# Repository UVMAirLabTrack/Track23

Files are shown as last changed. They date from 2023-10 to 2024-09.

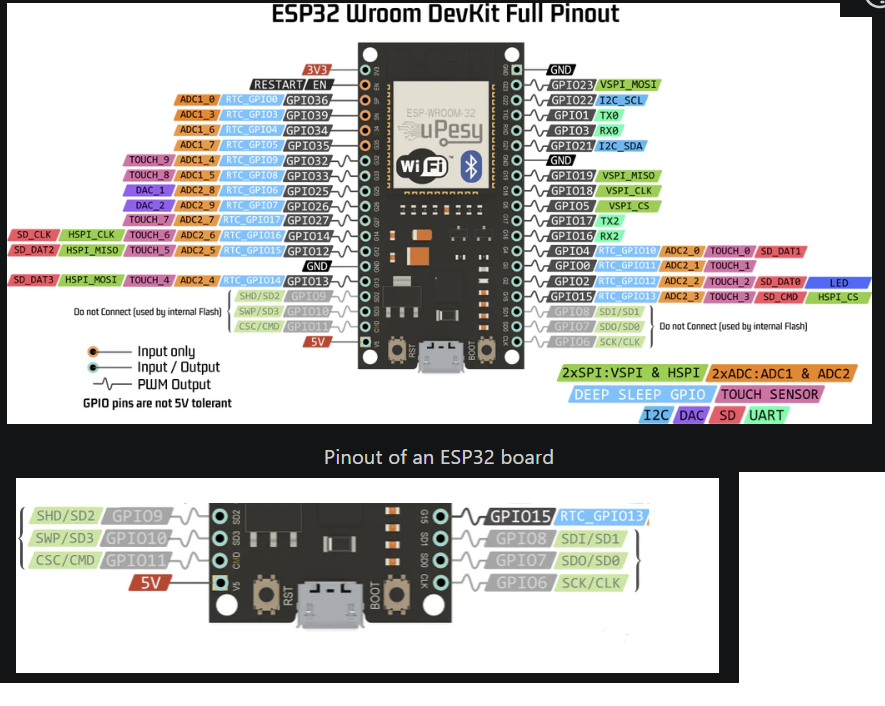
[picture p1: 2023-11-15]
InteractiveElements/Board Design and IO/ESP32GPIO.png

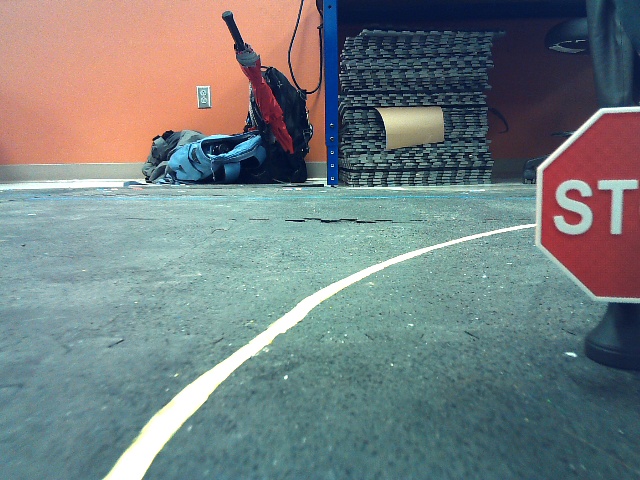
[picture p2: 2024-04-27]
Mid Process Stuff/Training Images/cut/stop (29).jpg

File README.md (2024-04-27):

# UVM SEED 2023 Track
 
## Repository for code and setup files associated with the 2023 UVM SEED Project for an urban track for autonomous cars

## File Structure

### A. Documentation
Look in here to find the detailed instructions on how to build and run the track system. As well as more in depth information as to the system's function

- 
- 
- 
- 

### 3D modelling

Under this folder are organized locations for all the .stl files used to create the various printed elements. 

### Interactive Elements

Here you will find the Arduino IDE code files used for the ESP32 interactive element network.
Additionally Kicad format PCB's and schematics are located here.
The receiver for each interactive element utilizes the same PCB, with 4 RJ45 connectors and a single ESP32 Dev Module with 38 pins (WROOM- D or E)
The only change is which code file is flashed. 

Some previous versions utilizing pure serial connections have been left for adapability. The latest track build utilizes:

1. Stoplight
    - ESPnow_4way_4int.ino  
    - ESP_now_3Way.ino
2. Train Crossing
    - ESPNowTrain_Complete.ino
3. Sender
    - ESPnowSender.ino

With the sender node being connected via serial to the computer controlling the track, In this case a Raspberry Pi 4B 8GB model.

### CoreRaspbery 
is the ROS2 Workspace,

at present the code is designed to build into a Humble distro, however in testing the code can also be built for a Foxy distro.

### Setup Files 
contains some basic files to aid in deploying the Raspberry Pi track computer

### Car commands 
is a curated list of the terminal commands needed to operate specific functions of the Yahboom R2 car
Also contained within are some quality of life improvements to the deployment of the docker environment on the car, just some simple .sh files.

### Other Code

A series of files not directly part of the track functionality. Mostly a series of HSV decoders and Webcam Capture files 

### files not in a folder

the Dockerfiles in the main directory are intended to build a docker container to run all the ROS code, this is not intended for deployment on the PI as of this moment, instead it is intended as a complete package for the vizualizer node(s). At present, windows communication via WiFi is not functional due to additional networking constraints.

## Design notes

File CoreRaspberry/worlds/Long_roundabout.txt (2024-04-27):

Change_Color False
X_position 0.0
Y_position 0.0
Z_position 0.0
Quaternion_x 0.0
Quaternion_y 0.0
Quaternion_z 0.0
Quaternion_w 1.0
Scale_x 1.0
Scale_y 1.0
Scale_z 1.0
Color_r 1.0
Color_g 1.0
Color_b 1.0
Color_a 1.0
Lifetime_sec 0
Frame_locked False
Mesh_use_embedded_materials True
Frame_id map

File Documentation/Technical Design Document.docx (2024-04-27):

Technical Design Document

_____________________________________________________________________________________

Date | Revision | Release Notes
4/26/24 | 01 | Initial Release

# 1 Mechanical Documentation

## 1.1 System Level Assembly Drawing 1: Interactive Urban Track

The System Level Assembly drawing of the project is shown in Figure 1 from the “System Level Diagram v1.dwg”.

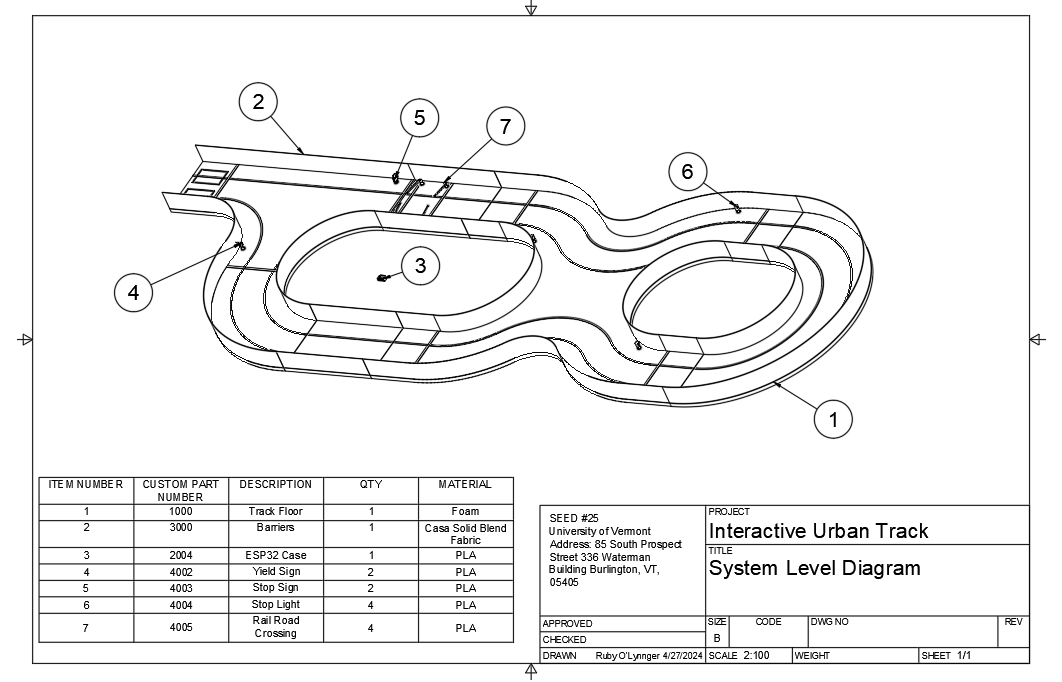
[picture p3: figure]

Figure 1 - System Level Assembly Drawing

## 1.2 System Level Bill of Materials

The System Level Bill of Materials is in Table 1, and also in the file “BOM.xlsx”.

Table 1 - Bill of Materials for Interactive Urban Track

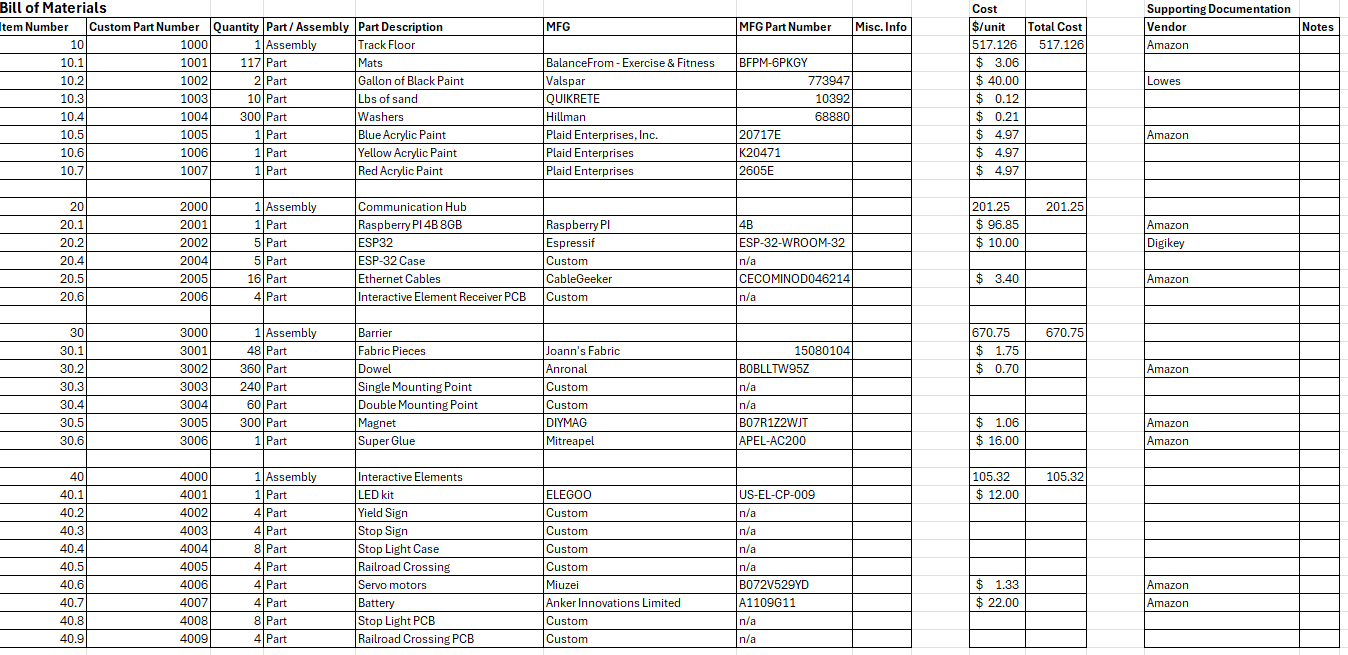
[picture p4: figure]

## 1.3 Part Drawings

### 1.3.1 Part 2004: ESP-32 Case

Part 2004: ESP-32 case is shown in Figure 2 from the file “ESP Controller Box Drawing.dwg”.

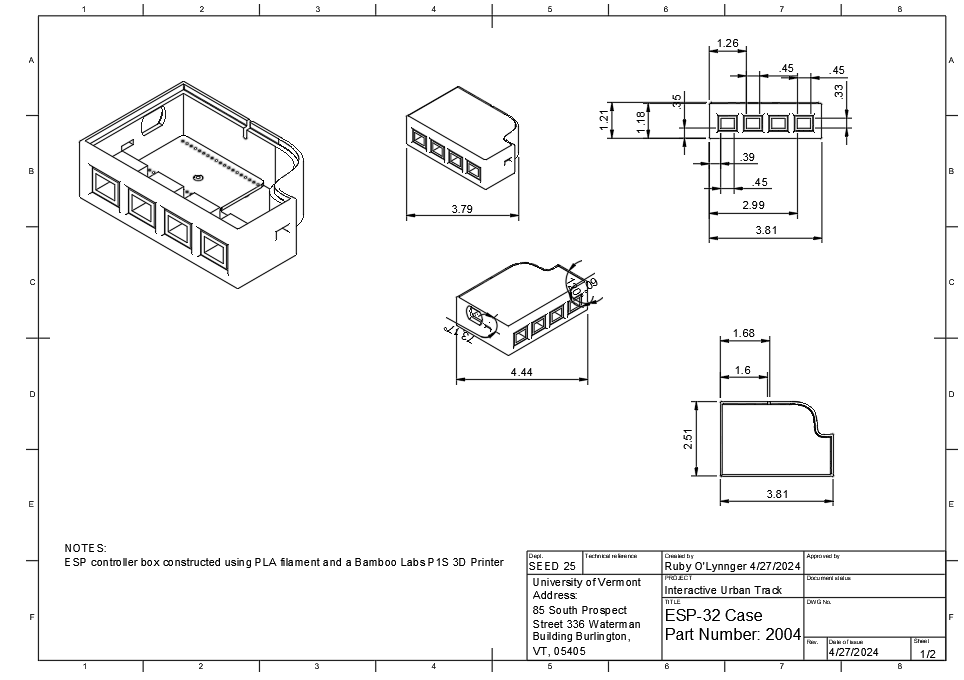
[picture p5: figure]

Figure 2 - ESP-32 Case Drawing

### 1.3.2 Part 3003: Single Mounting Point

Part 3003: Single Mounting Point is shown in Figure 3 from the file “Single Mounting Point Drawing v2.dwg”.

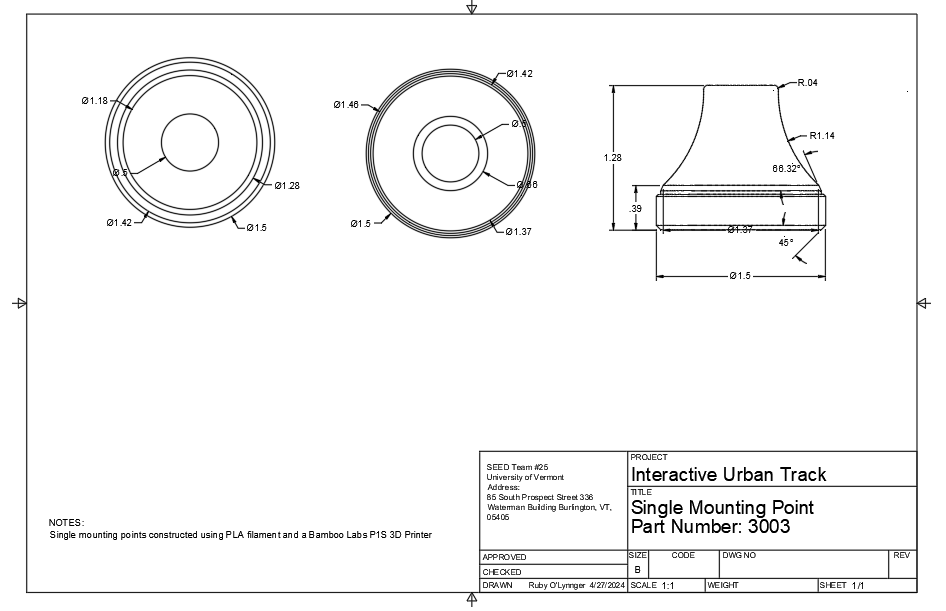
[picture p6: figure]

Figure 3 - Single Mounting Point Drawing

### 1.3.3 Part 3004: Double Mounting Point

Part 3004: Double Mounting Point is shown in Figure 4 from the file “Double Mounting Point Drawing v4.dwg”.

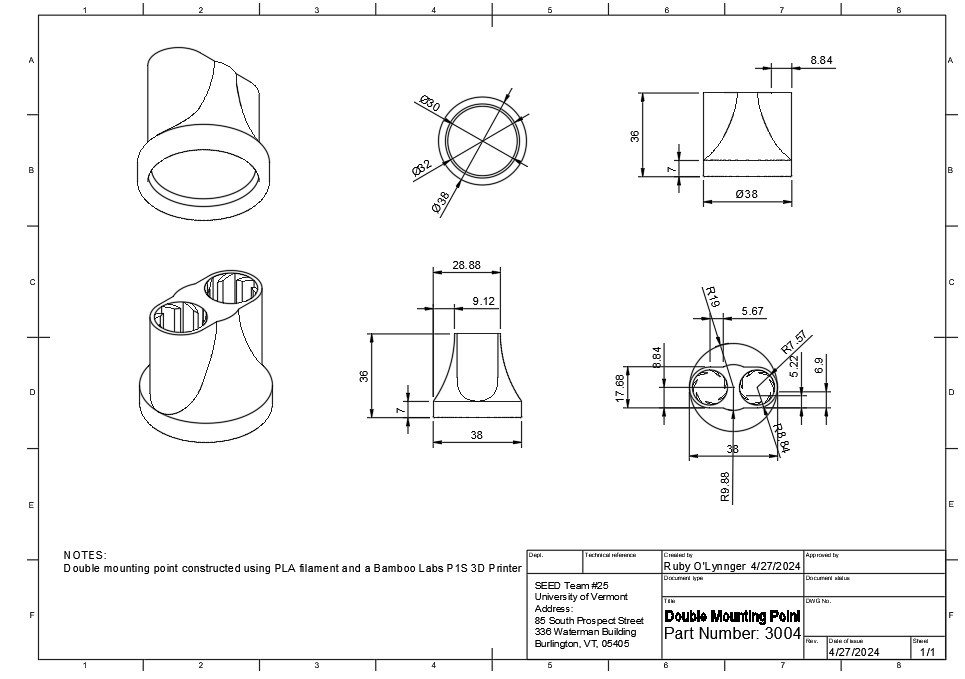
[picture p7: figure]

Figure 4 - Double Mounting Point Drawing

### 1.3.4 Part 4002: Yield Sign

Part 4002: Yield Sign is shown in Figure 5 from the file “Yield Sign Drawing.dwg”.

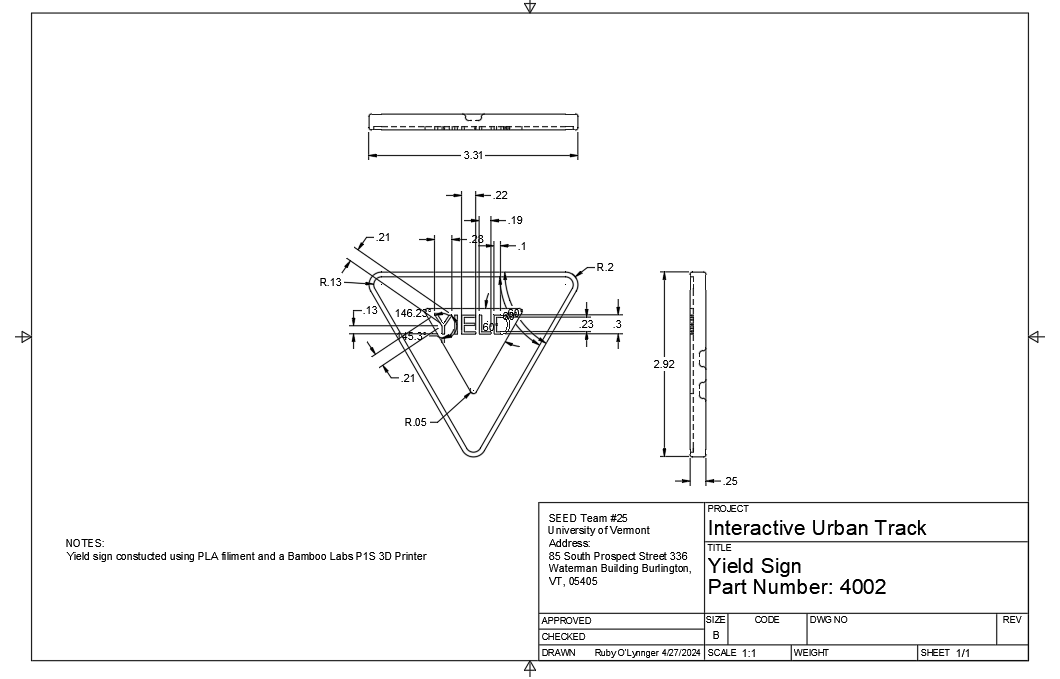
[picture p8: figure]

Figure 5 - Yield Sign Drawing

### 1.3.5 Part 4003: Stop Sign

Part 4003: Stop Sign is shown in Figure 6 from the file “Stop Sign Drawing.dwg”.

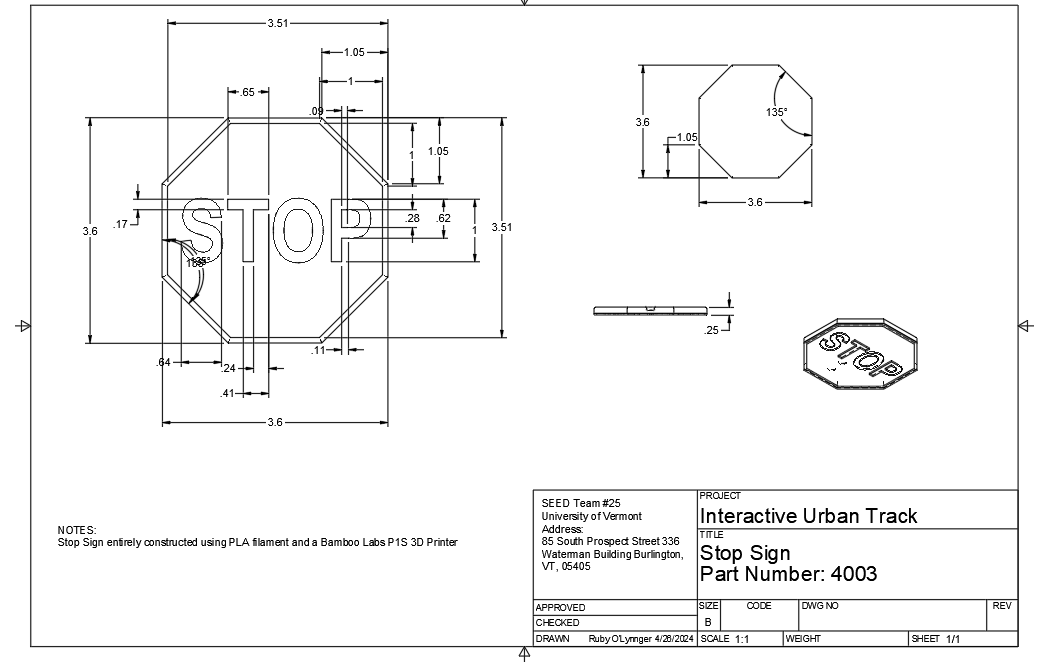
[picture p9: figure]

Figure 6 - Stop Sign Drawing

### 1.3.6 Part 4004: Stop Light

Part 4004: Stop Light is shown in Figure 7 from the file “Assembled Light Drawing v3.dwg”.

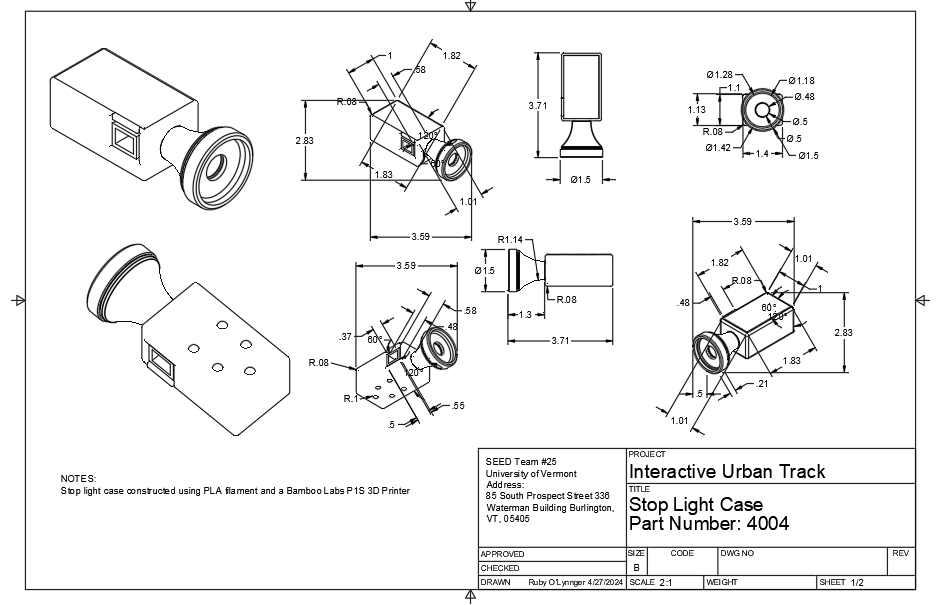
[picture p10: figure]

Figure 7 - Stop Light Drawing

### 1.3.7 Part 4005: Railroad Crossing

Part 4005: Railroad Crossing is shown in Figure 8 from the file “Assembled RR Barrier Drawing v2.dwg”.

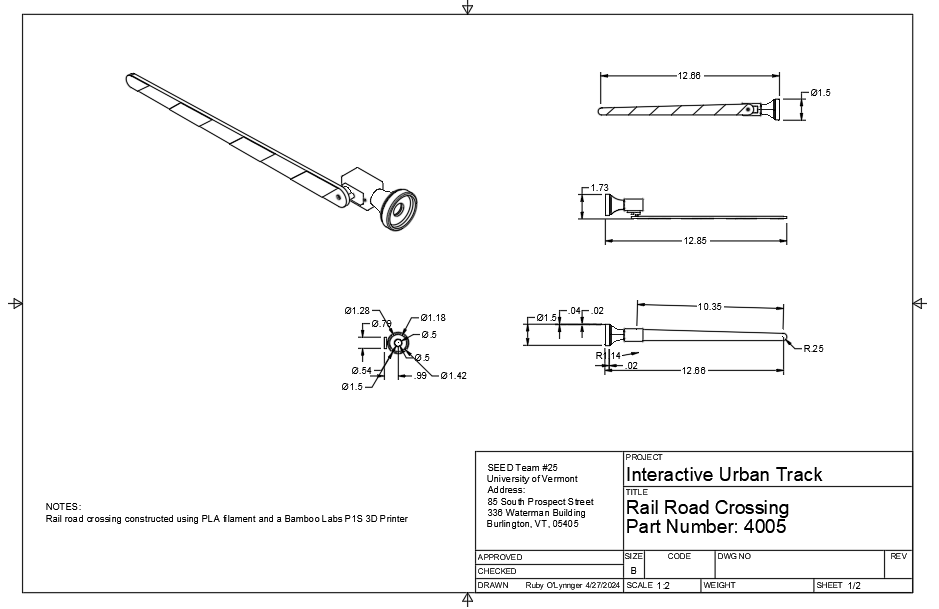
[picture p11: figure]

Figure 8 - Railroad Crossing Drawing

# 2 Electrical Documentation

## 2.1 System Level Wiring Diagram Drawing

The system level diagram is shown in

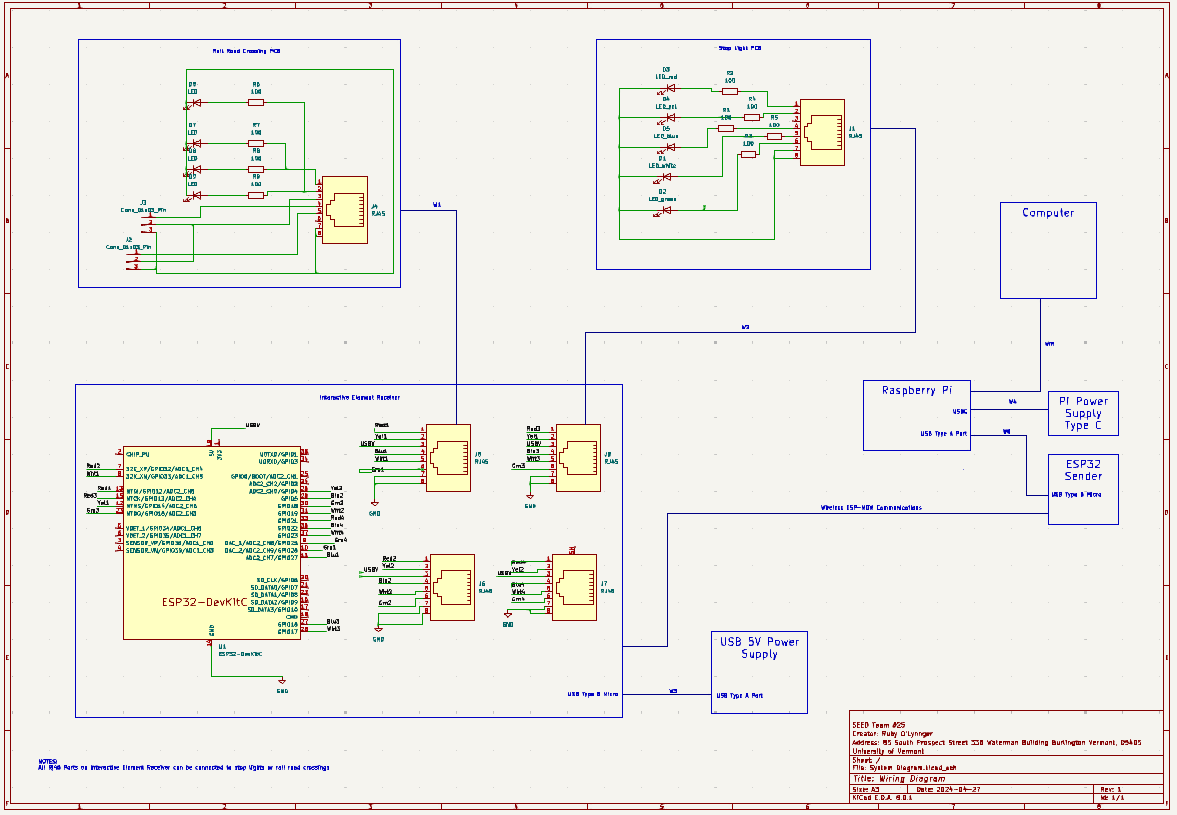
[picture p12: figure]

## 2.2 Wiring Diagram BoM

The wiring diagram BOM is shown in Table 2 from the file “Wiring_Diagram_BOM.xlsx”.

Table 2 - Wiring Diagram BOM

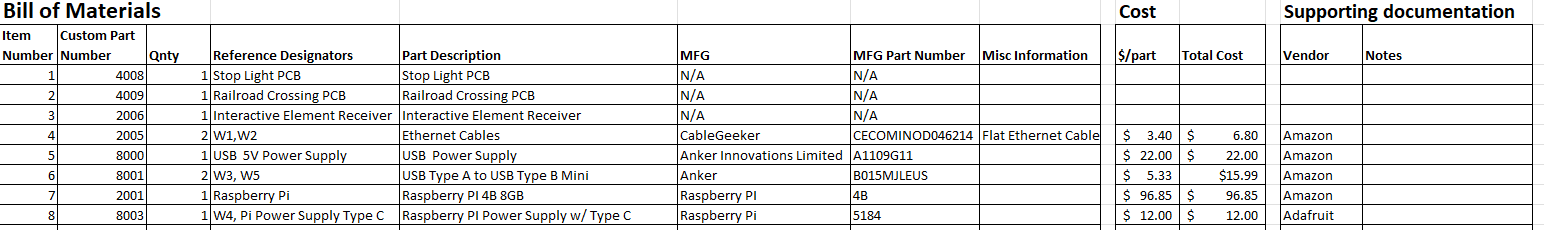
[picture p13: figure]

## 2.3 Printed Circuit Boards (PCB)

### 2.3.1 Stop Light PCB Schematic

Three custom PCBs were created for this project. The first one is the Stop Light PCB whose schematic can be seen in Figure 9 from the file “Light Pcb.kicad_sch”.

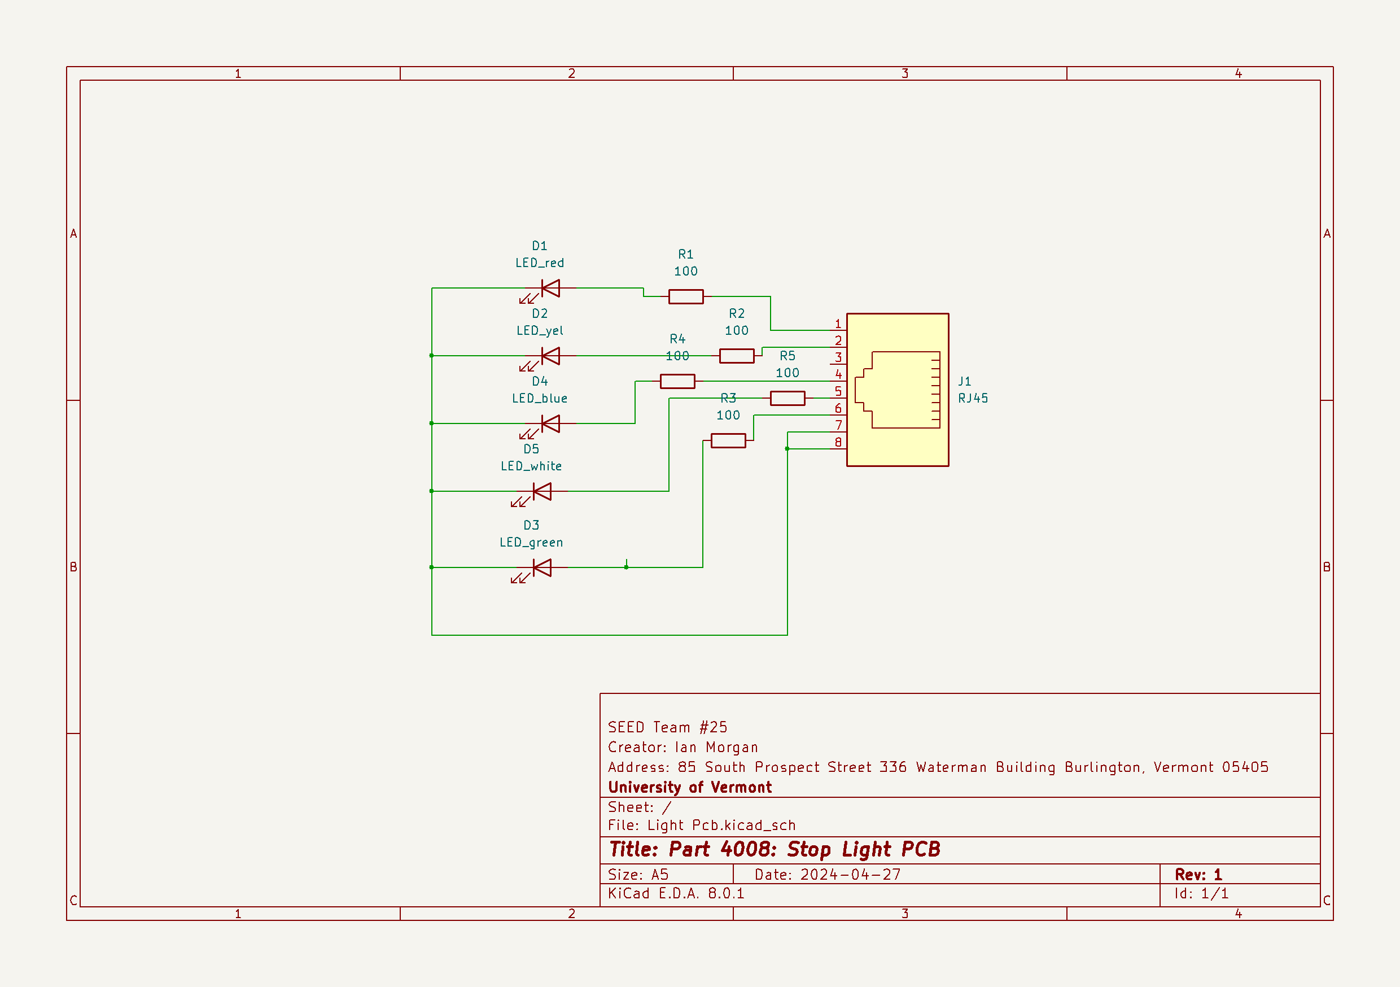
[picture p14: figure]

Figure 9 - Stop Light PCB Schematic

### 2.3.2 Stop Light PCB Layout Images

The overall layout of the Stop Light PCB can be seen in Figure 10 from the file “Light Pcb.kicad_pcb”.

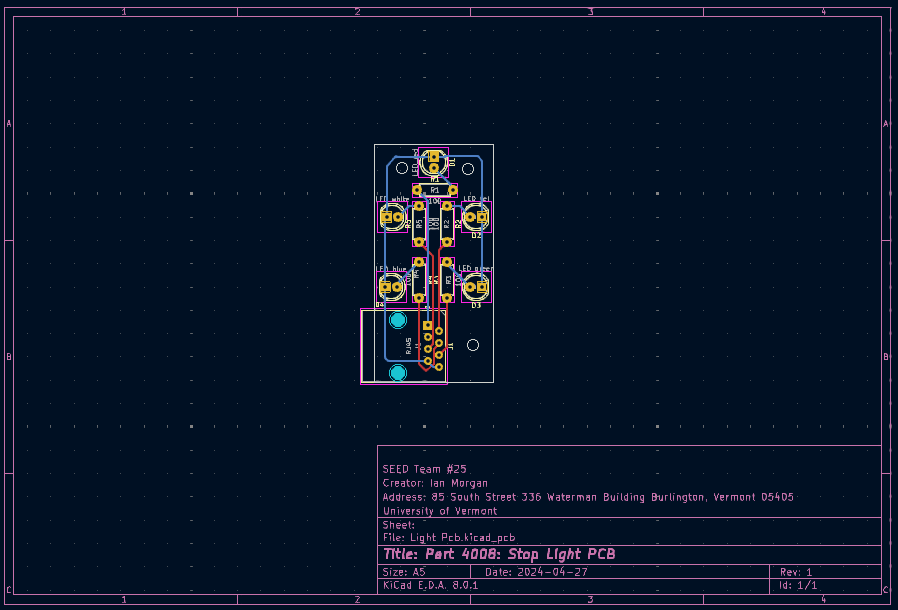
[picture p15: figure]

Figure 10 - Stop Light PCB Layout

### 2.3.3 Stop Light PCB Bill of Materials

The BOM for the Railroad Crossing PCB is shown in Table 3 from the file “StopLight _PCB_BOM.xlsx”.

Table 3 - Stop Light PCB Bill of Materials

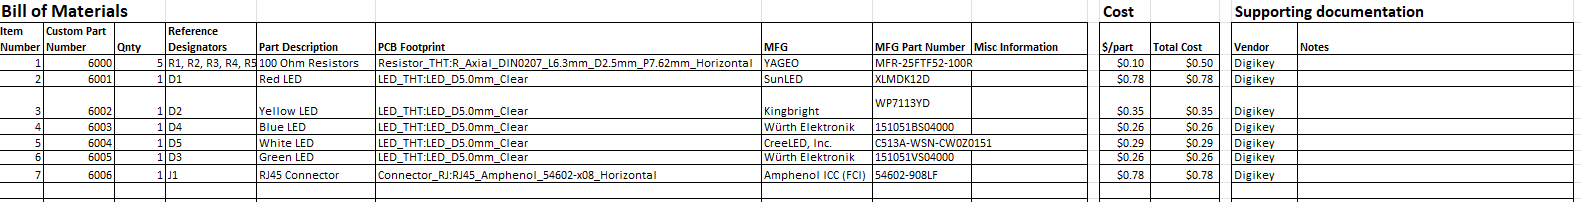
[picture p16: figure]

### 2.3.4 Railroad Crossing PCB Schematic

The second custom PCB is the Railroad Crossing PCB whose schematic can be seen in Figure 11 from the file “Servo_Adapt.kicad_sch”.

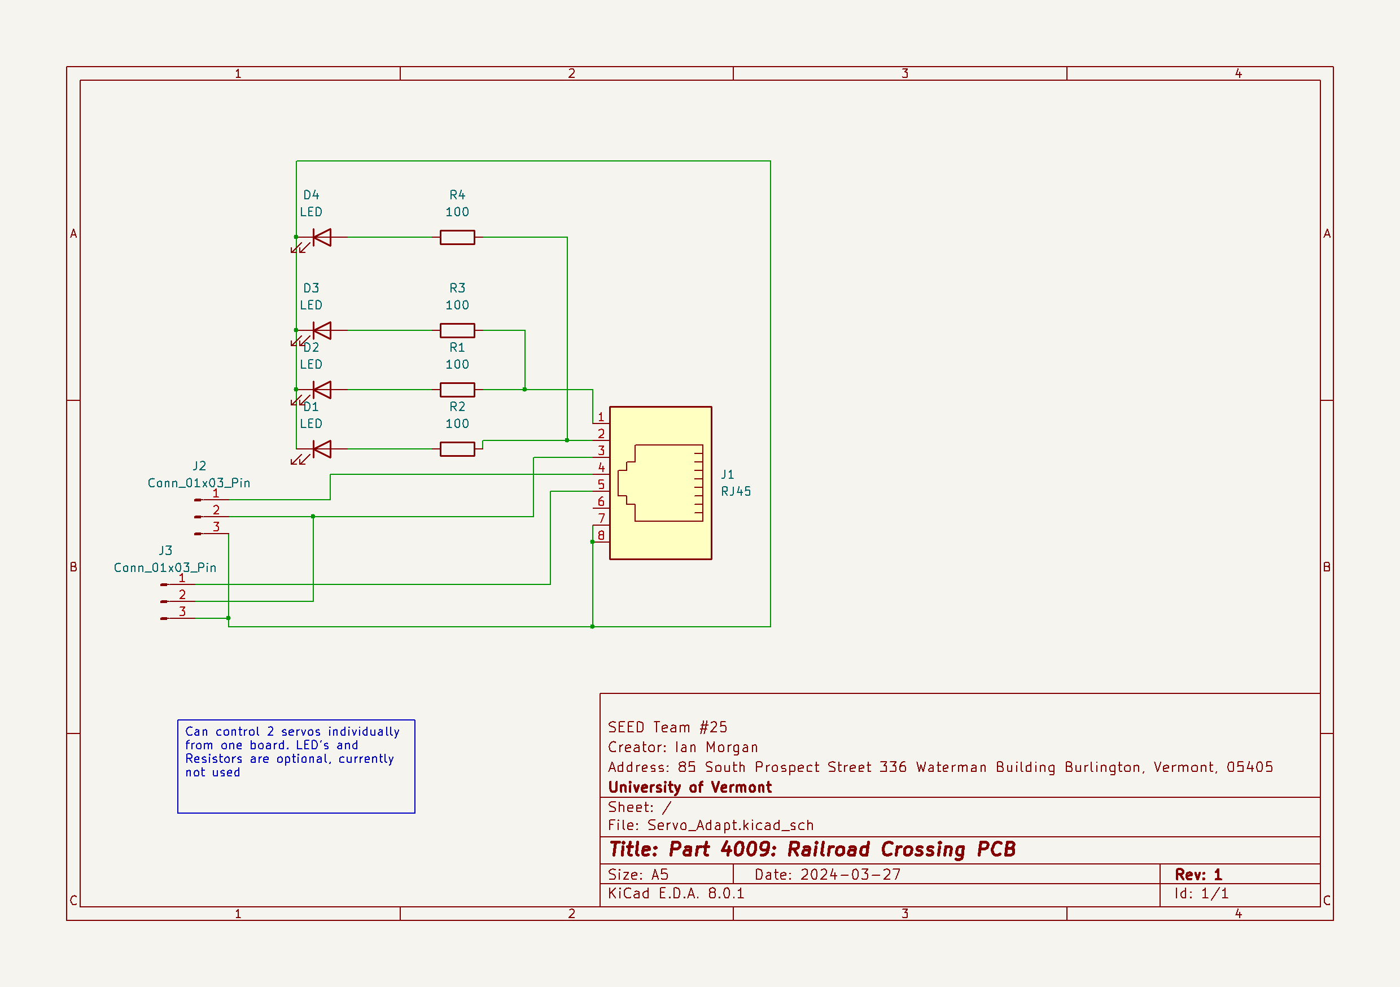
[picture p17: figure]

Figure 11 - Servo Adapter Schematic

### 2.3.5 Railroad Crossing PCB Layout Images

The overall layout of the Servo Adapter PCB can be seen in Figure 12 from the file “Servo_Adapt.kicad_pcb”.

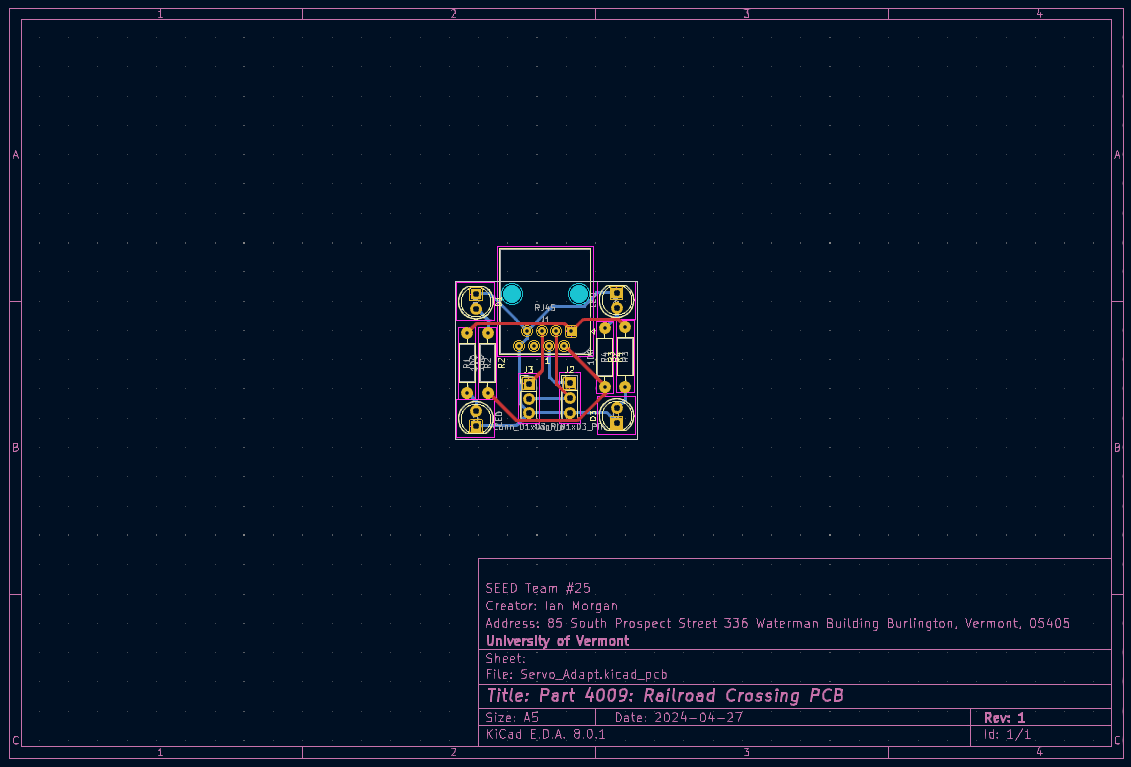
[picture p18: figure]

Figure 12 - Servo Adapter PCB Layout

### 2.3.6 Railroad Crossing PCB Bill of Materials

The BOM for the Railroad Crossing PCB is shown in Table 4 from the file “Railroad_Crossing_PCB_BOM.xlsx”.

Table 4 - Railroad Crossing PCB Bill of Materials

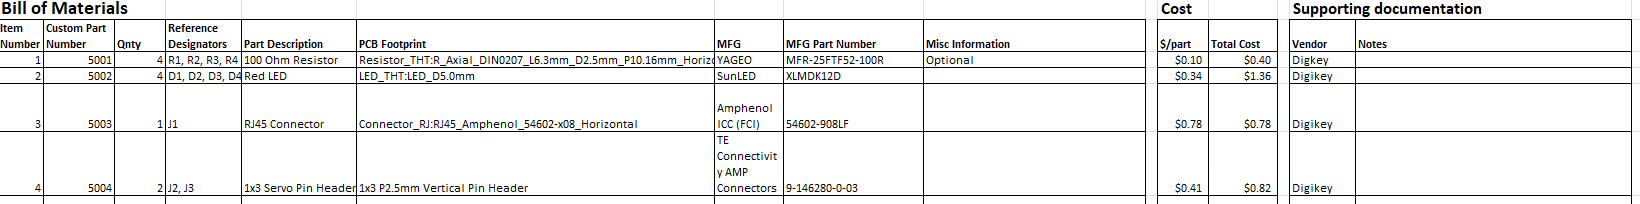
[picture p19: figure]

### 2.3.7 Interactive Element Receiver PCB Schematic

The final custom PCB that was made is the Interactive element PCB, whose schematic can be seen in Figure 13 from the file “Esp Controller.kicad_sch”.

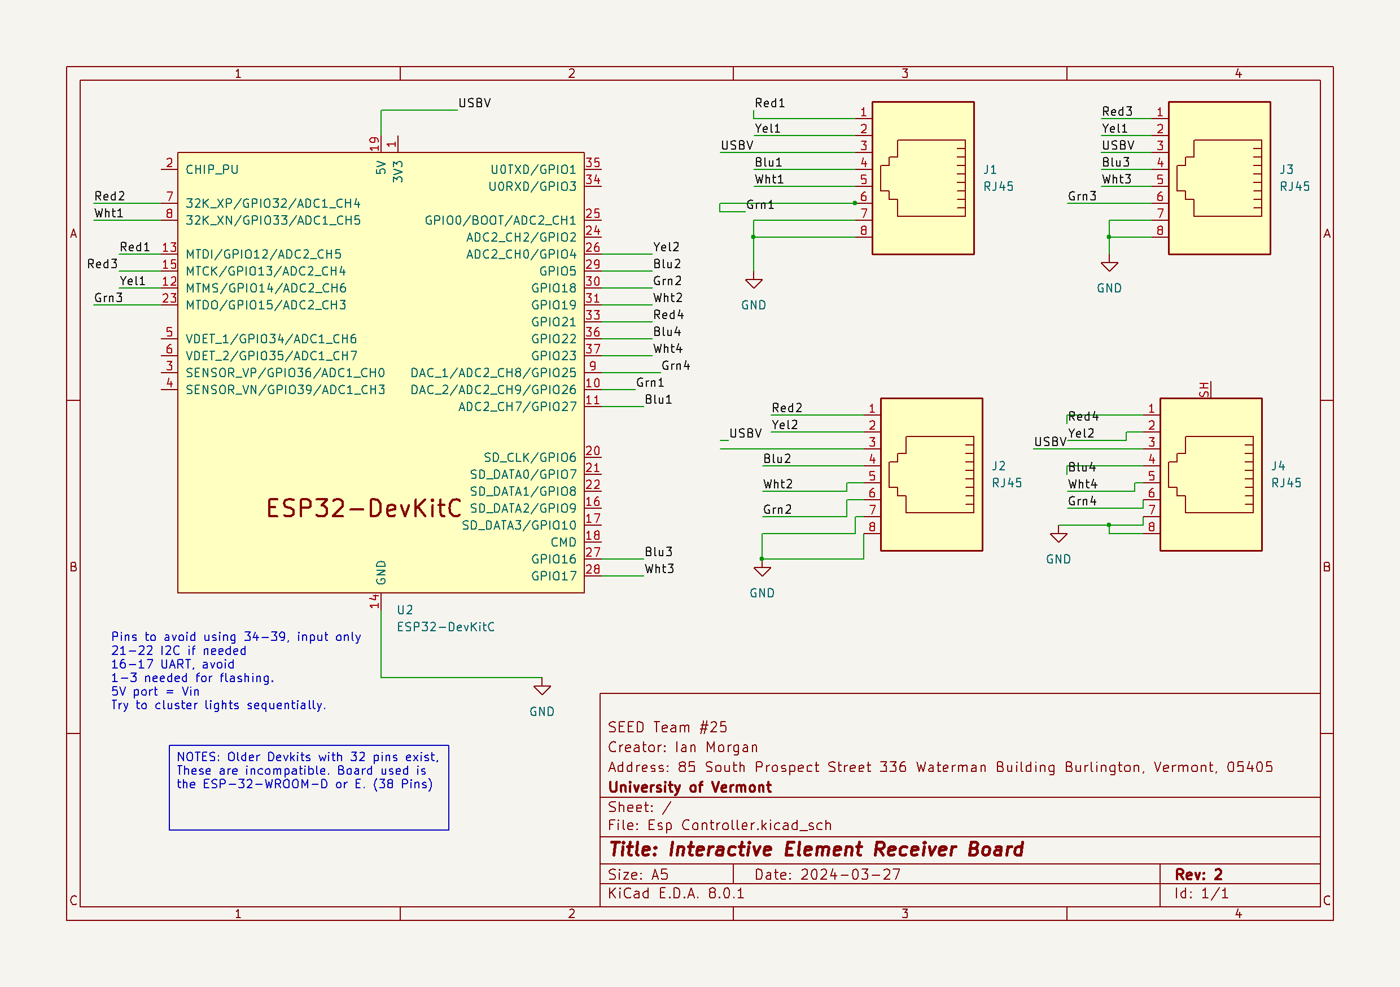
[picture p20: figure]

Figure 13 - Interactive Element Receiver Schematic

### 2.3.8 Interactive Element Receiver PCB Layout Images

The overall layout of the Interactive Element Receiver Board PCB can be seen in Figure 14 from the file “Esp Controller.kicad_pcb”.

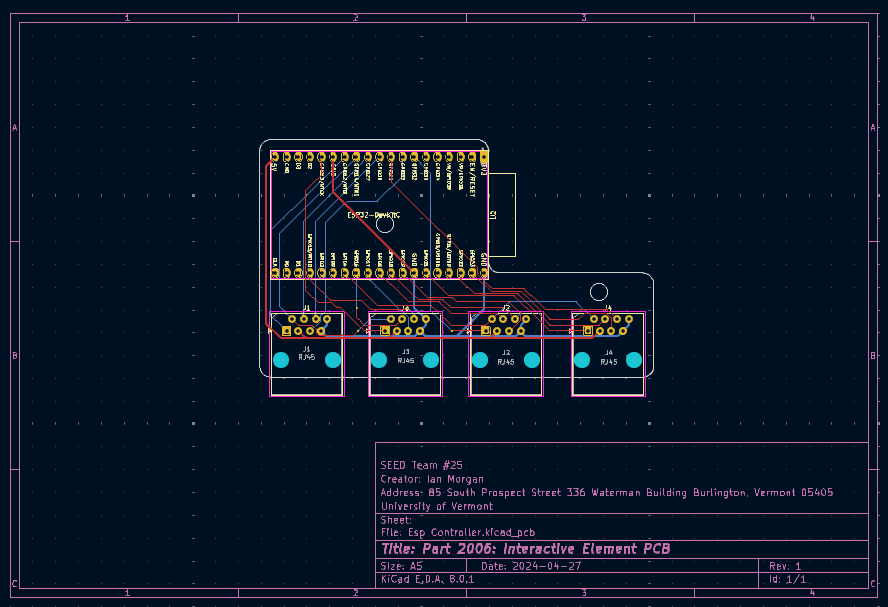
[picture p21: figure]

Figure 14 - Interactive Element Receiver Board

### 2.3.9 Interactive Element Receiver PCB Bill of Materials

The BOM for the Railroad Crossing PCB is shown in Table 5 from the file “Interactive_Element_PCB_BOM.xlsx”.

Table 5 - Interactive Element Receiver PCB Bill of Materials

# 3 Software Documentation

## 3.1 ESP Interactive element network

The interactive elements in the physical space are linked via a network of ESP-32 boards, connected via ESP-NOW protocol and serial communications via USB.

### 3.1.1 Instructions to Compile and Use

To Flash the Interactive Element Receiver (ESP Receiver) Simply select the desired function, eg Train Crossing. Open the file in Arduino IDE, with the Espressif Board Library installed as shown in Figure 15.

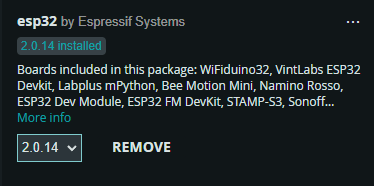
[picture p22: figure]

Figure 15 - Installed Espressif Board Library

Select the appropriate COM port from the top drop down menu as shown in Figure 16.

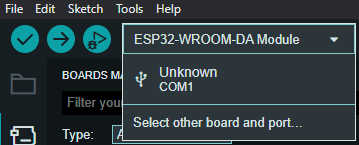
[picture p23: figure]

Figure 16 - COM Port Drop Down Menu

Type “wroom” in the boards search bar. Select the ESP32-WROOM-DA module, and the Com port. Select “Ok” as shown in Figure 17.

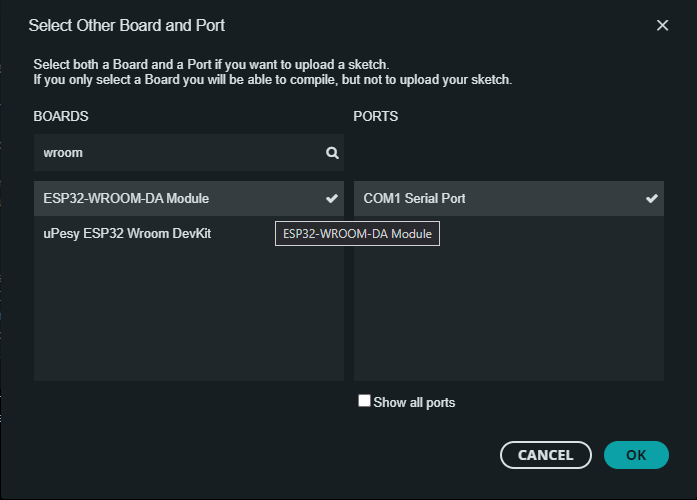
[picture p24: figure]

Figure 17 - Select OK

Then select “upload” (The Arrow button) as shown in Figure 18.

Figure 18 – Select Upload

Wait for the upload to complete, and that’s it.

Should the process fail, check the com port is correct, and in some cases the “boot” button on the ESP32 may need to be held down to load.

### 3.1.2 File Names and Purpose

  - Interactive Elements: Contains the Arduino code files, and PCBs for the physical interactive elements.
    - Animals: Contains the animal models for the track.
    - Board Design and IO: PCBs and associated Gerbers can be found here
    - DirectRemote: Code file for a remote control using the ESP Network, No ROS integration (Optional extra)
    - Driver for 38 pin board: Driver files to connect to the serial board on the ESP32
    - Files to start: Template Arduino files for ESP 32 receiver nodes.
    - Sender: The serial to ESP network bridge code. Connected to Pi via USB cable
    - Stoplight: Code for the ESP receiver for both 3 and 4 way light elements.
    - Train Crossing: Code for the ESP receiver for the movable train crossing element
    - Room dimensions v1: A 1:1 scale model in Fusion of Votey 308, with some immovable tables included.

## 3.2 ROS Code.

### 3.2.1 Directions for Initial Build

After installing Ubuntu 22.04 on the machine of choice.

1. Connect computer to Internet
2. Download and install NoMachine for the system architecture (AMD64 or ARM64)
3. Open a new terminal: Run this command set: this will pull down the github repo, with all the code for the car.
  a. git clone https://github.com/UVMAirLabTrack/Track23 RaspberryCore
  b. cd home/[user]/CoreRaspberry/Setup_files
  c. sudo chmod a+x control-install.sh Installs base software, suitable to a SBC or Pi
  d. Or sudo chmod a+x base-install.sh This installs a full software loadout, better suited to an x86 machine.
  e. Sudo chmod a+x ros-humble-std.sh This should install the full ROS2 Humble distribution
  f. cd /home/[user],RaspberryCore/CoreRaspberry/ Change your user to match
  g. colcon build --symlink-install This should build out the packages for the Pi. Once complete, you’re ready to run the worlds!
  h. Close the terminal. If you don’t things will appear to not work, the terminal does not live update settings.

### 3.2.2 Basic Use Instructions

Provided the setup has gone correctly, (This is open source software, compatibility is impossible to guarantee) These basic commands will get a world up and running. Note: All launch files are located under world_gen for simplicity. And for most commands, typing the first 3 letters then hitting tab for autocomplete is helpful.

1. Open a new terminal window for each separate command.
  a. ros2 launch world_gen track_launch Launches the Interactive network and serial coms.
  b. Ros2 launch world_gen all_viewer_launch Loads up RVIZ and the marker communication systems. Note, if the car marker is not visible, select “car” in the left pane, and adjust the topic to “carmesh_1” It should be visible in the pulldown menu.
  c. If you want to change the base track. Navigate to CoreRasperry/worlds and open world_select.txt. move the “y” to the desired world map. Then reload the all_viewer_launch command. (CTRL+C cancels running commands)

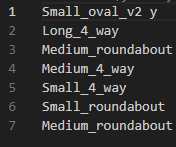
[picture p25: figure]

  d. Ros2 run map_transforms reset_car. This activates the ability to reset the car’s positional odometry with respect to the map. Press enter on the terminal window to activate, after 5 seconds the reset will stop collecting data and reflect the car’s return to the start location.
  e. To relocate interactive elements to different track positions open the respective [world]_markers.txt file. The structure used is [Topic,zone,location] . so the first element is which marker to display at a given location. Fourway_1 for example is the fourway light, element 1. 3way is the zone for the marker to be located in, in this case the 3 way intersection. The final location tag is which of the marker locations available at the 3 way to place it.

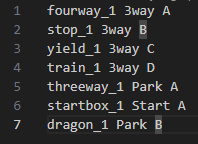
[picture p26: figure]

### 3.2.3 Code Structure

- Github Repository:
  - Car Commands: A set of text instruction files to deploy basic functions on the Yahboom R2 Car, commands are stock.
  - CoreRaspberry: This contains the code ROS code.
    - Build: Empty until package is deployed, will contain system level files
    - Control: The text files used to control the light and train states can be found here.
    - Example_package: exactly what it says, for building new packages in the future, might be better to reference an existing package at this point.
    - Install: empty until deployed, only for advanced users, direct edits not recommended
    - Log: log files
    - Src: source code. The python files and most reference files can be found here. Packages overview document lists the included packages and their file dependencies.
    - Worlds: contains the world mesh files, and the textual control files. For full details see packages overview document. For each world, here are the main files:
      - World.dae The actual world mesh file. New ones can be created by generating a 3d model in CAD of choice, exporting as a .obj file with meter scaling, then using blender to convert from .obj to .dae.
      - World.txt Contains the pose and color data for the world mesh.
      - World_markers.txt the reference file used to place a virtual element, at a specific location.
      - World_markers_loc.txt the coordinate position, angle, and zone for locations in the virtual space.
      - Markers: this folder contains a pose file for each individual marker used in the system.
  - Linux Commands: Some basic Linux script files to simplify deploying the environment.
  - Other Code: Python files not attached to ROS, such as HSV decoders, and Object detection files.
  - Setup Files: Text files for initial configuring of the Raspberry Pi.
  - Dockerfiles (not in a subfolder)
    - Dockerfile-r2-base: The base image provided with the R2 car. Here for reference.
    - Dockerfile-viz-r2-humble: Deploys the track visualizer environment on the R2 car. Pairs with the viz_bringup shell script in Linux commands.
    - Dockerfile-Viz-Humble: For deployment of the visualizer environment. Currently works with Linux, Networking with windows not yet functional, but otherwise can be run on windows as well.

# 4 Design Files

Table 6 - Design Files

Location | File Name | Description
EduSourced/Files/3D Models | AllTrackModels.zip | All solid models for the different track layouts for the project
EduSourced/Files/Design Files | AllTrackSectionModels.zip | All solid models for the track sections in the project
EduSourced/Files/Design Files | AllOtherModels.zip | All other solid models included in the track, including interactive elements and cases.
EduSourced/Files/Design Files | Drawings.zip | All drawing files for custom parts and system level overview.
EduSourced/Files/BOM | Interactive_Element_ Receiver_PCB_BOM.xlsx | BOM for the Interactive Element Receiver PCB
EduSourced/Files/BOM | Railroad_Crossing_ PCB_BOM.xlsx | BOM for the Railroad Crossing PCB
EduSourced/Files/BOM | StopLight_PCB_BOM.xlsx | BOM for the Stop Light PCB
EduSourced/Files/BOM | Wiring_Diagram_BOM.xlsx | BOM for the Wiring Diagram
EduSourced/Files/BOM | BOM.xlsx | BOM for entire system
EduSourced/Files/PCBs | InteractiveElement Receiver.zip | All design and Gerber files for Interactive Element Receiver PCB
EduSourced/Files/PCBs | RailroadCrossing.zip | All design and Gerber files for Railroad Crossing PCB
EduSourced/Files/PCBs | StopLightPCB.zip | All design and Gerber files for Stop Light PCB
EduSourced/Files/PCBs | System Diagram.zip | Wiring Diagram schematic
https://github.com/ UVMAirLabTrack/Track23.git | All Code | All files and packages listed in the Software section and in the user manual.
EduSourced/Files/ | Setup Manual.docx | User Manual

# 5 User Operation Manual

A User Operation Manual has been written to instruct future users how to set up and operate the project. This manual is the file “Setup Manual.docx”. It contains all physical track setup information and a more in depth explanation of the software section in this document.

Project #25 Technical Design Document9

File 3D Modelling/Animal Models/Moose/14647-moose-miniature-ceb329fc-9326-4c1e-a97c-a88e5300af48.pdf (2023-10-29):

3D MODEL ONLY

# Summary

This is a remix of the model located here by lodkylo : http://www.thingiverse.com/thing:191957 Its a moose perfect for...

Toys & Games (https://www.printables.com/model?categoryId=30) > Board Games (https://www.printables.com/model?categoryId=31)

Tags: moose | mount | dnd | dungeonsanddragons

This is a remix of the model located here by lodkylo : http://www.thingiverse.com/thing:191957

Its a moose perfect for a tabletop game as a mount. Print the body as is with supports and a raft. Print the head with supports and a raft as well.

Want to access even more models not found here in Prusa Printers? Interested in supporting my efforts making free models for the world to enjoy? Check out my patreon page here: https://www.patreon.com/mz4250

Patrons have access to all my files in one place, a request board, as well as commercial and commission options! Come check it out :-)

## Print instructions

Unassociated tags: d&d
Category: Games

MZ4250 (https://www.printables.com/social/39782/about)

# Moose Miniature

VIEW IN BROWSER (https://www.printables.com/model/14647-moose-miniature)

updated 12. 4. 2022 | published 19. 12. 2019

# Model files

Find source .stl files on Thingiverse.com (https://www.thingiverse.com/thing:1923436)

# License

This work is licensed under a
Creative Commons (4.0 International License)

Attribution (http://creativecommons.org/licenses/by/4.0/)

✖ | Sharing without ATTRIBUTION
✔ | Remix Culture allowed
✔ | Commercial Use
✔ | Free Cultural Works
✔ | Meets Open Definition

moose_body.stl

moose_head.stl

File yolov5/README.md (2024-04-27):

<div align="center">
  <p>
    <a href="http://www.ultralytics.com/blog/ultralytics-yolov8-turns-one-a-year-of-breakthroughs-and-innovations" target="_blank">
      </a>
    <!--
    <a align="center" href="https://ultralytics.com/yolov5" target="_blank">
      <img width="100%" src="https://raw.githubusercontent.com/ultralytics/assets/main/yolov5/v70/splash.png"></a>
    -->
  </p>

[中文](https://docs.ultralytics.com/zh/) | [한국어](https://docs.ultralytics.com/ko/) | [日本語](https://docs.ultralytics.com/ja/) | [Русский](https://docs.ultralytics.com/ru/) | [Deutsch](https://docs.ultralytics.com/de/) | [Français](https://docs.ultralytics.com/fr/) | [Español](https://docs.ultralytics.com/es/) | [Português](https://docs.ultralytics.com/pt/) | [हिन्दी](https://docs.ultralytics.com/hi/) | [العربية](https://docs.ultralytics.com/ar/)

<div>
    
    
    
    
    <br>
    
    
    <a href="https://www.kaggle.com/ultralytics/yolov5">Open In Kaggle</a>
  </div>
  <br>

YOLOv5 🚀 is the world's most loved vision AI, representing <a href="https://ultralytics.com">Ultralytics</a> open-source research into future vision AI methods, incorporating lessons learned and best practices evolved over thousands of hours of research and development.

We hope that the resources here will help you get the most out of YOLOv5. Please browse the YOLOv5 <a href="https://docs.ultralytics.com/yolov5">Docs</a> for details, raise an issue on <a href="https://github.com/ultralytics/yolov5/issues/new/choose">GitHub</a> for support, and join our <a href="https://ultralytics.com/discord">Discord</a> community for questions and discussions!

To request an Enterprise License please complete the form at [Ultralytics Licensing](https://ultralytics.com/license).

<div align="center">
  <a href="https://github.com/ultralytics">Ultralytics GitHub</a>
  
  <a href="https://www.linkedin.com/company/ultralytics/">Ultralytics LinkedIn</a>
  
  <a href="https://twitter.com/ultralytics">Ultralytics Twitter</a>
  
  <a href="https://youtube.com/ultralytics">Ultralytics YouTube</a>
  
  <a href="https://www.tiktok.com/@ultralytics">Ultralytics TikTok</a>
  
  <a href="https://www.instagram.com/ultralytics/">Ultralytics Instagram</a>
  
  <a href="https://ultralytics.com/discord">Ultralytics Discord</a>
</div>

</div>
<br>

## <div align="center">YOLOv8 🚀 NEW</div>

We are thrilled to announce the launch of Ultralytics YOLOv8 🚀, our NEW cutting-edge, state-of-the-art (SOTA) model released at **[https://github.com/ultralytics/ultralytics](https://github.com/ultralytics/ultralytics)**. YOLOv8 is designed to be fast, accurate, and easy to use, making it an excellent choice for a wide range of object detection, image segmentation and image classification tasks.

See the [YOLOv8 Docs](https://docs.ultralytics.com) for details and get started with:

 

```bash
pip install ultralytics
```

<div align="center">
  <a href="https://ultralytics.com/yolov8" target="_blank">
  </a>
</div>

## <div align="center">Documentation</div>

See the [YOLOv5 Docs](https://docs.ultralytics.com/yolov5) for full documentation on training, testing and deployment. See below for quickstart examples.

<details open>
<summary>Install</summary>

Clone repo and install [requirements.txt](https://github.com/ultralytics/yolov5/blob/master/requirements.txt) in a [**Python>=3.8.0**](https://www.python.org/) environment, including [**PyTorch>=1.8**](https://pytorch.org/get-started/locally/).

```bash
git clone https://github.com/ultralytics/yolov5  # clone
cd yolov5
pip install -r requirements.txt  # install
```

</details>

<details>
<summary>Inference</summary>

YOLOv5 [PyTorch Hub](https://docs.ultralytics.com/yolov5/tutorials/pytorch_hub_model_loading) inference. [Models](https://github.com/ultralytics/yolov5/tree/master/models) download automatically from the latest YOLOv5 [release](https://github.com/ultralytics/yolov5/releases).

```python
import torch

# Model
model = torch.hub.load("ultralytics/yolov5", "yolov5s")  # or yolov5n - yolov5x6, custom

# Images
img = "https://ultralytics.com/images/zidane.jpg"  # or file, Path, PIL, OpenCV, numpy, list

# Inference
results = model(img)

# Results
results.print()  # or .show(), .save(), .crop(), .pandas(), etc.
```

</details>

<details>
<summary>Inference with detect.py</summary>

`detect.py` runs inference on a variety of sources, downloading [models](https://github.com/ultralytics/yolov5/tree/master/models) automatically from the latest YOLOv5 [release](https://github.com/ultralytics/yolov5/releases) and saving results to `runs/detect`.

```bash
python detect.py --weights yolov5s.pt --source 0                               # webcam
                                               img.jpg                         # image
                                               vid.mp4                         # video
                                               screen                          # screenshot
                                               path/                           # directory
                                               list.txt                        # list of images
                                               list.streams                    # list of streams
                                               'path/*.jpg'                    # glob
                                               'https://youtu.be/LNwODJXcvt4'  # YouTube
                                               'rtsp://example.com/media.mp4'  # RTSP, RTMP, HTTP stream
```

</details>

<details>
<summary>Training</summary>

The commands below reproduce YOLOv5 [COCO](https://github.com/ultralytics/yolov5/blob/master/data/scripts/get_coco.sh) results. [Models](https://github.com/ultralytics/yolov5/tree/master/models) and [datasets](https://github.com/ultralytics/yolov5/tree/master/data) download automatically from the latest YOLOv5 [release](https://github.com/ultralytics/yolov5/releases). Training times for YOLOv5n/s/m/l/x are 1/2/4/6/8 days on a V100 GPU ([Multi-GPU](https://docs.ultralytics.com/yolov5/tutorials/multi_gpu_training) times faster). Use the largest `--batch-size` possible, or pass `--batch-size -1` for YOLOv5 [AutoBatch](https://github.com/ultralytics/yolov5/pull/5092). Batch sizes shown for V100-16GB.

```bash
python train.py --data coco.yaml --epochs 300 --weights '' --cfg yolov5n.yaml  --batch-size 128
                                                                 yolov5s                    64
                                                                 yolov5m                    40
                                                                 yolov5l                    24
                                                                 yolov5x                    16
```



</details>

<details open>
<summary>Tutorials</summary>

- [Train Custom Data](https://docs.ultralytics.com/yolov5/tutorials/train_custom_data) 🚀 RECOMMENDED
- [Tips for Best Training Results](https://docs.ultralytics.com/yolov5/tutorials/tips_for_best_training_results) ☘️
- [Multi-GPU Training](https://docs.ultralytics.com/yolov5/tutorials/multi_gpu_training)
- [PyTorch Hub](https://docs.ultralytics.com/yolov5/tutorials/pytorch_hub_model_loading) 🌟 NEW
- [TFLite, ONNX, CoreML, TensorRT Export](https://docs.ultralytics.com/yolov5/tutorials/model_export) 🚀
- [NVIDIA Jetson platform Deployment](https://docs.ultralytics.com/yolov5/tutorials/running_on_jetson_nano) 🌟 NEW
- [Test-Time Augmentation (TTA)](https://docs.ultralytics.com/yolov5/tutorials/test_time_augmentation)
- [Model Ensembling](https://docs.ultralytics.com/yolov5/tutorials/model_ensembling)
- [Model Pruning/Sparsity](https://docs.ultralytics.com/yolov5/tutorials/model_pruning_and_sparsity)
- [Hyperparameter Evolution](https://docs.ultralytics.com/yolov5/tutorials/hyperparameter_evolution)
- [Transfer Learning with Frozen Layers](https://docs.ultralytics.com/yolov5/tutorials/transfer_learning_with_frozen_layers)
- [Architecture Summary](https://docs.ultralytics.com/yolov5/tutorials/architecture_description) 🌟 NEW
- [Roboflow for Datasets, Labeling, and Active Learning](https://docs.ultralytics.com/yolov5/tutorials/roboflow_datasets_integration)
- [ClearML Logging](https://docs.ultralytics.com/yolov5/tutorials/clearml_logging_integration) 🌟 NEW
- [YOLOv5 with Neural Magic's Deepsparse](https://docs.ultralytics.com/yolov5/tutorials/neural_magic_pruning_quantization) 🌟 NEW
- [Comet Logging](https://docs.ultralytics.com/yolov5/tutorials/comet_logging_integration) 🌟 NEW

</details>

## <div align="center">Integrations</div>

<br>
<a align="center" href="https://bit.ly/ultralytics_hub" target="_blank">
</a>
<br>
<br>

<div align="center">
  <a href="https://roboflow.com/?ref=ultralytics">
    </a>
  
  <a href="https://cutt.ly/yolov5-readme-clearml">
    </a>
  
  <a href="https://bit.ly/yolov5-readme-comet2">
    </a>
  
  <a href="https://bit.ly/yolov5-neuralmagic">
    </a>
</div>

| Roboflow | ClearML ⭐ NEW | Comet ⭐ NEW | Neural Magic ⭐ NEW |
| :---: | :---: | :---: | :---: |
| Label and export your custom datasets directly to YOLOv5 for training with [Roboflow](https://roboflow.com/?ref=ultralytics) | Automatically track, visualize and even remotely train YOLOv5 using [ClearML](https://cutt.ly/yolov5-readme-clearml) (open-source!) | Free forever, [Comet](https://bit.ly/yolov5-readme-comet2) lets you save YOLOv5 models, resume training, and interactively visualise and debug predictions | Run YOLOv5 inference up to 6x faster with [Neural Magic DeepSparse](https://bit.ly/yolov5-neuralmagic) |

## <div align="center">Ultralytics HUB</div>

Experience seamless AI with [Ultralytics HUB](https://bit.ly/ultralytics_hub) ⭐, the all-in-one solution for data visualization, YOLOv5 and YOLOv8 🚀 model training and deployment, without any coding. Transform images into actionable insights and bring your AI visions to life with ease using our cutting-edge platform and user-friendly [Ultralytics App](https://ultralytics.com/app_install). Start your journey for **Free** now!

<a align="center" href="https://bit.ly/ultralytics_hub" target="_blank">
</a>

## <div align="center">Why YOLOv5</div>

YOLOv5 has been designed to be super easy to get started and simple to learn. We prioritize real-world results.


<details>
  <summary>YOLOv5-P5 640 Figure</summary>


</details>
<details>
  <summary>Figure Notes</summary>

- **COCO AP val** denotes mAP@0.5:0.95 metric measured on the 5000-image [COCO val2017](http://cocodataset.org) dataset over various inference sizes from 256 to 1536.
- **GPU Speed** measures average inference time per image on [COCO val2017](http://cocodataset.org) dataset using a [AWS p3.2xlarge](https://aws.amazon.com/ec2/instance-types/p3/) V100 instance at batch-size 32.
- **EfficientDet** data from [google/automl](https://github.com/google/automl) at batch size 8.
- **Reproduce** by `python val.py --task study --data coco.yaml --iou 0.7 --weights yolov5n6.pt yolov5s6.pt yolov5m6.pt yolov5l6.pt yolov5x6.pt`

</details>

### Pretrained Checkpoints

| Model | size<br><sup>(pixels) | mAP<sup>val<br>50-95 | mAP<sup>val<br>50 | Speed<br><sup>CPU b1<br>(ms) | Speed<br><sup>V100 b1<br>(ms) | Speed<br><sup>V100 b32<br>(ms) | params<br><sup>(M) | FLOPs<br><sup>@640 (B) |
| --- | --- | --- | --- | --- | --- | --- | --- | --- |
| [YOLOv5n](https://github.com/ultralytics/yolov5/releases/download/v7.0/yolov5n.pt) | 640 | 28.0 | 45.7 | **45** | **6.3** | **0.6** | **1.9** | **4.5** |
| [YOLOv5s](https://github.com/ultralytics/yolov5/releases/download/v7.0/yolov5s.pt) | 640 | 37.4 | 56.8 | 98 | 6.4 | 0.9 | 7.2 | 16.5 |
| [YOLOv5m](https://github.com/ultralytics/yolov5/releases/download/v7.0/yolov5m.pt) | 640 | 45.4 | 64.1 | 224 | 8.2 | 1.7 | 21.2 | 49.0 |
| [YOLOv5l](https://github.com/ultralytics/yolov5/releases/download/v7.0/yolov5l.pt) | 640 | 49.0 | 67.3 | 430 | 10.1 | 2.7 | 46.5 | 109.1 |
| [YOLOv5x](https://github.com/ultralytics/yolov5/releases/download/v7.0/yolov5x.pt) | 640 | 50.7 | 68.9 | 766 | 12.1 | 4.8 | 86.7 | 205.7 |
| | | | | | | | | |
| [YOLOv5n6](https://github.com/ultralytics/yolov5/releases/download/v7.0/yolov5n6.pt) | 1280 | 36.0 | 54.4 | 153 | 8.1 | 2.1 | 3.2 | 4.6 |
| [YOLOv5s6](https://github.com/ultralytics/yolov5/releases/download/v7.0/yolov5s6.pt) | 1280 | 44.8 | 63.7 | 385 | 8.2 | 3.6 | 12.6 | 16.8 |
| [YOLOv5m6](https://github.com/ultralytics/yolov5/releases/download/v7.0/yolov5m6.pt) | 1280 | 51.3 | 69.3 | 887 | 11.1 | 6.8 | 35.7 | 50.0 |
| [YOLOv5l6](https://github.com/ultralytics/yolov5/releases/download/v7.0/yolov5l6.pt) | 1280 | 53.7 | 71.3 | 1784 | 15.8 | 10.5 | 76.8 | 111.4 |
| [YOLOv5x6](https://github.com/ultralytics/yolov5/releases/download/v7.0/yolov5x6.pt)<br>+ [TTA] | 1280<br>1536 | 55.0<br>**55.8** | 72.7<br>**72.7**  | 3136<br>- | 26.2<br>- | 19.4<br>- | 140.7<br>- | 209.8<br>- |

<details>
  <summary>Table Notes</summary>

- All checkpoints are trained to 300 epochs with default settings. Nano and Small models use [hyp.scratch-low.yaml](https://github.com/ultralytics/yolov5/blob/master/data/hyps/hyp.scratch-low.yaml) hyps, all others use [hyp.scratch-high.yaml](https://github.com/ultralytics/yolov5/blob/master/data/hyps/hyp.scratch-high.yaml).
- **mAP<sup>val</sup>** values are for single-model single-scale on [COCO val2017](http://cocodataset.org) dataset.<br>Reproduce by `python val.py --data coco.yaml --img 640 --conf 0.001 --iou 0.65`
- **Speed** averaged over COCO val images using a [AWS p3.2xlarge](https://aws.amazon.com/ec2/instance-types/p3/) instance. NMS times (~1 ms/img) not included.<br>Reproduce by `python val.py --data coco.yaml --img 640 --task speed --batch 1`
- **TTA** [Test Time Augmentation](https://docs.ultralytics.com/yolov5/tutorials/test_time_augmentation) includes reflection and scale augmentations.<br>Reproduce by `python val.py --data coco.yaml --img 1536 --iou 0.7 --augment`

</details>

## <div align="center">Segmentation</div>

Our new YOLOv5 [release v7.0](https://github.com/ultralytics/yolov5/releases/v7.0) instance segmentation models are the fastest and most accurate in the world, beating all current [SOTA benchmarks](https://paperswithcode.com/sota/real-time-instance-segmentation-on-mscoco). We've made them super simple to train, validate and deploy. See full details in our [Release Notes](https://github.com/ultralytics/yolov5/releases/v7.0) and visit our [YOLOv5 Segmentation Colab Notebook](https://github.com/ultralytics/yolov5/blob/master/segment/tutorial.ipynb) for quickstart tutorials.

<details>
  <summary>Segmentation Checkpoints</summary>

<div align="center">
<a align="center" href="https://ultralytics.com/yolov5" target="_blank">
</a>
</div>

We trained YOLOv5 segmentations models on COCO for 300 epochs at image size 640 using A100 GPUs. We exported all models to ONNX FP32 for CPU speed tests and to TensorRT FP16 for GPU speed tests. We ran all speed tests on Google [Colab Pro](https://colab.research.google.com/signup) notebooks for easy reproducibility.

| Model | size<br><sup>(pixels) | mAP<sup>box<br>50-95 | mAP<sup>mask<br>50-95 | Train time<br><sup>300 epochs<br>A100 (hours) | Speed<br><sup>ONNX CPU<br>(ms) | Speed<br><sup>TRT A100<br>(ms) | params<br><sup>(M) | FLOPs<br><sup>@640 (B) |
| --- | --- | --- | --- | --- | --- | --- | --- | --- |
| [YOLOv5n-seg](https://github.com/ultralytics/yolov5/releases/download/v7.0/yolov5n-seg.pt) | 640 | 27.6 | 23.4 | 80:17 | **62.7** | **1.2** | **2.0** | **7.1** |
| [YOLOv5s-seg](https://github.com/ultralytics/yolov5/releases/download/v7.0/yolov5s-seg.pt) | 640 | 37.6 | 31.7 | 88:16 | 173.3 | 1.4 | 7.6 | 26.4 |
| [YOLOv5m-seg](https://github.com/ultralytics/yolov5/releases/download/v7.0/yolov5m-seg.pt) | 640 | 45.0 | 37.1 | 108:36 | 427.0 | 2.2 | 22.0 | 70.8 |
| [YOLOv5l-seg](https://github.com/ultralytics/yolov5/releases/download/v7.0/yolov5l-seg.pt) | 640 | 49.0 | 39.9 | 66:43 (2x) | 857.4 | 2.9 | 47.9 | 147.7 |
| [YOLOv5x-seg](https://github.com/ultralytics/yolov5/releases/download/v7.0/yolov5x-seg.pt) | 640 | **50.7** | **41.4** | 62:56 (3x) | 1579.2 | 4.5 | 88.8 | 265.7 |

- All checkpoints are trained to 300 epochs with SGD optimizer with `lr0=0.01` and `weight_decay=5e-5` at image size 640 and all default settings.<br>Runs logged to https://wandb.ai/glenn-jocher/YOLOv5_v70_official
- **Accuracy** values are for single-model single-scale on COCO dataset.<br>Reproduce by `python segment/val.py --data coco.yaml --weights yolov5s-seg.pt`
- **Speed** averaged over 100 inference images using a [Colab Pro](https://colab.research.google.com/signup) A100 High-RAM instance. Values indicate inference speed only (NMS adds about 1ms per image). <br>Reproduce by `python segment/val.py --data coco.yaml --weights yolov5s-seg.pt --batch 1`
- **Export** to ONNX at FP32 and TensorRT at FP16 done with `export.py`. <br>Reproduce by `python export.py --weights yolov5s-seg.pt --include engine --device 0 --half`

</details>

<details>
  <summary>Segmentation Usage Examples &nbsp;</summary>

### Train

YOLOv5 segmentation training supports auto-download COCO128-seg segmentation dataset with `--data coco128-seg.yaml` argument and manual download of COCO-segments dataset with `bash data/scripts/get_coco.sh --train --val --segments` and then `python train.py --data coco.yaml`.

```bash
# Single-GPU
python segment/train.py --data coco128-seg.yaml --weights yolov5s-seg.pt --img 640

# Multi-GPU DDP
python -m torch.distributed.run --nproc_per_node 4 --master_port 1 segment/train.py --data coco128-seg.yaml --weights yolov5s-seg.pt --img 640 --device 0,1,2,3
```

### Val

Validate YOLOv5s-seg mask mAP on COCO dataset:

```bash
bash data/scripts/get_coco.sh --val --segments  # download COCO val segments split (780MB, 5000 images)
python segment/val.py --weights yolov5s-seg.pt --data coco.yaml --img 640  # validate
```

### Predict

Use pretrained YOLOv5m-seg.pt to predict bus.jpg:

```bash
python segment/predict.py --weights yolov5m-seg.pt --source data/images/bus.jpg
```

```python
model = torch.hub.load(
    "ultralytics/yolov5", "custom", "yolov5m-seg.pt"
)  # load from PyTorch Hub (WARNING: inference not yet supported)
```

| zidane | bus |
| --- | --- |

### Export

Export YOLOv5s-seg model to ONNX and TensorRT:

```bash
python export.py --weights yolov5s-seg.pt --include onnx engine --img 640 --device 0
```

</details>

## <div align="center">Classification</div>

YOLOv5 [release v6.2](https://github.com/ultralytics/yolov5/releases) brings support for classification model training, validation and deployment! See full details in our [Release Notes](https://github.com/ultralytics/yolov5/releases/v6.2) and visit our [YOLOv5 Classification Colab Notebook](https://github.com/ultralytics/yolov5/blob/master/classify/tutorial.ipynb) for quickstart tutorials.

<details>
  <summary>Classification Checkpoints</summary>

<br>

We trained YOLOv5-cls classification models on ImageNet for 90 epochs using a 4xA100 instance, and we trained ResNet and EfficientNet models alongside with the same default training settings to compare. We exported all models to ONNX FP32 for CPU speed tests and to TensorRT FP16 for GPU speed tests. We ran all speed tests on Google [Colab Pro](https://colab.research.google.com/signup) for easy reproducibility.

| Model | size<br><sup>(pixels) | acc<br><sup>top1 | acc<br><sup>top5 | Training<br><sup>90 epochs<br>4xA100 (hours) | Speed<br><sup>ONNX CPU<br>(ms) | Speed<br><sup>TensorRT V100<br>(ms) | params<br><sup>(M) | FLOPs<br><sup>@224 (B) |
| --- | --- | --- | --- | --- | --- | --- | --- | --- |
| [YOLOv5n-cls](https://github.com/ultralytics/yolov5/releases/download/v7.0/yolov5n-cls.pt) | 224 | 64.6 | 85.4 | 7:59 | **3.3** | **0.5** | **2.5** | **0.5** |
| [YOLOv5s-cls](https://github.com/ultralytics/yolov5/releases/download/v7.0/yolov5s-cls.pt) | 224 | 71.5 | 90.2 | 8:09 | 6.6 | 0.6 | 5.4 | 1.4 |
| [YOLOv5m-cls](https://github.com/ultralytics/yolov5/releases/download/v7.0/yolov5m-cls.pt) | 224 | 75.9 | 92.9 | 10:06 | 15.5 | 0.9 | 12.9 | 3.9 |
| [YOLOv5l-cls](https://github.com/ultralytics/yolov5/releases/download/v7.0/yolov5l-cls.pt) | 224 | 78.0 | 94.0 | 11:56 | 26.9 | 1.4 | 26.5 | 8.5 |
| [YOLOv5x-cls](https://github.com/ultralytics/yolov5/releases/download/v7.0/yolov5x-cls.pt) | 224 | **79.0** | **94.4** | 15:04 | 54.3 | 1.8 | 48.1 | 15.9 |
| | | | | | | | | |
| [ResNet18](https://github.com/ultralytics/yolov5/releases/download/v7.0/resnet18.pt) | 224 | 70.3 | 89.5 | **6:47** | 11.2 | 0.5 | 11.7 | 3.7 |
| [ResNet34](https://github.com/ultralytics/yolov5/releases/download/v7.0/resnet34.pt) | 224 | 73.9 | 91.8 | 8:33 | 20.6 | 0.9 | 21.8 | 7.4 |
| [ResNet50](https://github.com/ultralytics/yolov5/releases/download/v7.0/resnet50.pt) | 224 | 76.8 | 93.4 | 11:10 | 23.4 | 1.0 | 25.6 | 8.5 |
| [ResNet101](https://github.com/ultralytics/yolov5/releases/download/v7.0/resnet101.pt) | 224 | 78.5 | 94.3 | 17:10 | 42.1 | 1.9 | 44.5 | 15.9 |
| | | | | | | | | |
| [EfficientNet_b0](https://github.com/ultralytics/yolov5/releases/download/v7.0/efficientnet_b0.pt) | 224 | 75.1 | 92.4 | 13:03 | 12.5 | 1.3 | 5.3 | 1.0 |
| [EfficientNet_b1](https://github.com/ultralytics/yolov5/releases/download/v7.0/efficientnet_b1.pt) | 224 | 76.4 | 93.2 | 17:04 | 14.9 | 1.6 | 7.8 | 1.5 |
| [EfficientNet_b2](https://github.com/ultralytics/yolov5/releases/download/v7.0/efficientnet_b2.pt) | 224 | 76.6 | 93.4 | 17:10 | 15.9 | 1.6 | 9.1 | 1.7 |
| [EfficientNet_b3](https://github.com/ultralytics/yolov5/releases/download/v7.0/efficientnet_b3.pt) | 224 | 77.7 | 94.0 | 19:19 | 18.9 | 1.9 | 12.2 | 2.4 |

<details>
  <summary>Table Notes (click to expand)</summary>

- All checkpoints are trained to 90 epochs with SGD optimizer with `lr0=0.001` and `weight_decay=5e-5` at image size 224 and all default settings.<br>Runs logged to https://wandb.ai/glenn-jocher/YOLOv5-Classifier-v6-2
- **Accuracy** values are for single-model single-scale on [ImageNet-1k](https://www.image-net.org/index.php) dataset.<br>Reproduce by `python classify/val.py --data ../datasets/imagenet --img 224`
- **Speed** averaged over 100 inference images using a Google [Colab Pro](https://colab.research.google.com/signup) V100 High-RAM instance.<br>Reproduce by `python classify/val.py --data ../datasets/imagenet --img 224 --batch 1`
- **Export** to ONNX at FP32 and TensorRT at FP16 done with `export.py`. <br>Reproduce by `python export.py --weights yolov5s-cls.pt --include engine onnx --imgsz 224`

</details>
</details>

<details>
  <summary>Classification Usage Examples &nbsp;</summary>

### Train

YOLOv5 classification training supports auto-download of MNIST, Fashion-MNIST, CIFAR10, CIFAR100, Imagenette, Imagewoof, and ImageNet datasets with the `--data` argument. To start training on MNIST for example use `--data mnist`.

```bash
# Single-GPU
python classify/train.py --model yolov5s-cls.pt --data cifar100 --epochs 5 --img 224 --batch 128

# Multi-GPU DDP
python -m torch.distributed.run --nproc_per_node 4 --master_port 1 classify/train.py --model yolov5s-cls.pt --data imagenet --epochs 5 --img 224 --device 0,1,2,3
```

### Val

Validate YOLOv5m-cls accuracy on ImageNet-1k dataset:

```bash
bash data/scripts/get_imagenet.sh --val  # download ImageNet val split (6.3G, 50000 images)
python classify/val.py --weights yolov5m-cls.pt --data ../datasets/imagenet --img 224  # validate
```

### Predict

Use pretrained YOLOv5s-cls.pt to predict bus.jpg:

```bash
python classify/predict.py --weights yolov5s-cls.pt --source data/images/bus.jpg
```

```python
model = torch.hub.load(
    "ultralytics/yolov5", "custom", "yolov5s-cls.pt"
)  # load from PyTorch Hub
```

### Export

Export a group of trained YOLOv5s-cls, ResNet and EfficientNet models to ONNX and TensorRT:

```bash
python export.py --weights yolov5s-cls.pt resnet50.pt efficientnet_b0.pt --include onnx engine --img 224
```

</details>

## <div align="center">Environments</div>

Get started in seconds with our verified environments. Click each icon below for details.

<div align="center">
  <a href="https://bit.ly/yolov5-paperspace-notebook">
    </a>
  
  <a href="https://colab.research.google.com/github/ultralytics/yolov5/blob/master/tutorial.ipynb">
    </a>
  
  <a href="https://www.kaggle.com/ultralytics/yolov5">
    </a>
  
  <a href="https://hub.docker.com/r/ultralytics/yolov5">
    </a>
  
  <a href="https://docs.ultralytics.com/yolov5/environments/aws_quickstart_tutorial/">
    </a>
  
  <a href="https://docs.ultralytics.com/yolov5/environments/google_cloud_quickstart_tutorial/">
    </a>
</div>

## <div align="center">Contribute</div>

We love your input! We want to make contributing to YOLOv5 as easy and transparent as possible. Please see our [Contributing Guide](https://docs.ultralytics.com/help/contributing/) to get started, and fill out the [YOLOv5 Survey](https://ultralytics.com/survey?utm_source=github&utm_medium=social&utm_campaign=Survey) to send us feedback on your experiences. Thank you to all our contributors!

<!-- SVG image from https://opencollective.com/ultralytics/contributors.svg?width=990 -->

<a href="https://github.com/ultralytics/yolov5/graphs/contributors">
</a>

## <div align="center">License</div>

Ultralytics offers two licensing options to accommodate diverse use cases:

- **AGPL-3.0 License**: This [OSI-approved](https://opensource.org/licenses/) open-source license is ideal for students and enthusiasts, promoting open collaboration and knowledge sharing. See the [LICENSE](https://github.com/ultralytics/yolov5/blob/master/LICENSE) file for more details.
- **Enterprise License**: Designed for commercial use, this license permits seamless integration of Ultralytics software and AI models into commercial goods and services, bypassing the open-source requirements of AGPL-3.0. If your scenario involves embedding our solutions into a commercial offering, reach out through [Ultralytics Licensing](https://ultralytics.com/license).

## <div align="center">Contact</div>

For YOLOv5 bug reports and feature requests please visit [GitHub Issues](https://github.com/ultralytics/yolov5/issues), and join our [Discord](https://ultralytics.com/discord) community for questions and discussions!

<br>
<div align="center">
  <a href="https://github.com/ultralytics">Ultralytics GitHub</a>
  
  <a href="https://www.linkedin.com/company/ultralytics/">Ultralytics LinkedIn</a>
  
  <a href="https://twitter.com/ultralytics">Ultralytics Twitter</a>
  
  <a href="https://youtube.com/ultralytics">Ultralytics YouTube</a>
  
  <a href="https://www.tiktok.com/@ultralytics">Ultralytics TikTok</a>
  
  <a href="https://www.instagram.com/ultralytics/">Ultralytics Instagram</a>
  
  <a href="https://ultralytics.com/discord">Ultralytics Discord</a>
</div>

[tta]: https://docs.ultralytics.com/yolov5/tutorials/test_time_augmentation

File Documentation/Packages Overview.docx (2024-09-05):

# List of ROS2 packages and functions

# Launch Files

All contained under the world_gen package.

all_viewer_launch: This boots up the visualizer node, with all marker types enabled. Including the stoplights, signs, train crossing, and dragon. Also boots up the odom_to_map_key executable to transform the car odometry to the map. And the Gen_v2 to create the world mesh

Within, the various labelled publishers will display status messages.

Packages utilized:

- World_gen: Four_Way_marker
- World_gen: Three_Way_marker
- World_gen: Stop_sign
- World_gen: Yield_Sign
- World_gen: Train_marker
- Map_transforms: Odom_to_map_key
- World_gen: Gen_v2
- Xcore2: pub_All_pose

Track_launch: Loads up the three_way, four_way and train control signal publishers, As well as the ESP_serial node, which performs serial to wireless communications. This file is intended to be run on the Pi, or whatever computer you are utilizing to connect to the ESP network. Published state messages are shown in the terminal window.

Packages utilized:

- Four_way_light: gen
- three_way_light: gen
- train_crossing: gen
- direct_io: esp_serial

Train_viewer_launch: Similar to All_viewer_launch, except only the train crossing markers are loaded.

Light_viewer_launch: similar to all_viewer_launch, except only the 3 and 4 way lights are loaded.

At present, all viewer launch files utilize the same RVIZ configuration file, in the future it is suggested to build thinner and lighter versions for each configuration.

# Interactive Controls.

## Four_way_light

Code File: pub.py

Ros Build name: pub

Published topic(s): four_way_state

Subscription topic(s): None

Reference files: light_states_4.txt

This package contains a single core file, “pub”

The function is to parse the reference file of light states, and pass them along the topic in the structure of a 4 integer array to control the stoplight in the real and virtual space.

That array looks like: [Light1, Light2, Light3, Light4]

At present only 4 states are utilized, with the rest existing for expansion.

They are:

- 0: All Lights Off
- 1: “Red” Uses a pattern of the Red, White, and Blue LED’s illuminated
- 2: “Yellow” Only the yellow LED is illuminated
- 3: “Green” The Green and Blue LED’s are illuminated

To change the light patterns: enter the CoreRaspberry/control folder, and edit “light_tates_4.txt” Opening the file will look something like the figure below:


The system takes the first 4 numbers in a row, and sets the control variables for the lights, publishes, then waits the number of seconds specified by the 5th number in the row. Then moves to the next line. Then cycles back to the first entry when the last is reached.

## Three_way_light

Code File: pub.py

Ros Build name: pub

Published topic(s): three_way_state

Subscription topic(s): None

Reference files: light_states_3.txt

The function is to parse the reference file of light states, and pass them along the topic in the structure of a 4 integer array to control the stoplight in the real and virtual space.

That array looks like: [Light1, Light2, Light3, Light4]

At present only 4 states are utilized, with the rest existing for expansion.

They are:

- 0: All Lights Off
- 1: “Red” Uses a pattern of the Red, White, and Blue LED’s illuminated
- 2: “Yellow” Only the yellow LED is illuminated
- 3: “Green” The Green and Blue LED’s are illuminated

To change the light patterns: enter the CoreRaspberry/control folder, and edit “light_tates_3.txt” Opening the file will look something like the figure below:

The system takes the first 4 numbers in a row, and sets the control variables for the lights, publishes, then waits the number of seconds specified by the 5th number in the row. Then moves to the next line. Then cycles back to the first entry when the last is reached.

## Train_crossing

Code File: pub.py

Ros Build name: pub

Published topic(s): train_crossing_state

Subscription topic(s): None

Reference files: train_states.txt

The function is to parse the reference file of crossing states, and pass them along the topic in the structure of a 4 integer array to control the barrier in the real and virtual space.

That array looks like: [Barrier1, Barrier2, Barrier3, Barrier4]

Each barrier state refers to an angle in degrees. With 0 being down, angles up to 180 are possible, but will likely run into obstruction by the fabric “Lidar fence”.

To change the barrier patterns: enter the CoreRaspberry/control folder, and edit “train_states.txt” Opening the file will look something like the figure below:


The system takes the first 4 numbers in a row, and sets the control variables for the barriers, publishes, then waits the number of seconds specified by the 5th number in the row. Then moves to the next line. Then cycles back to the first entry when the last is reached.

## Direct_io

Code File: esp_serial.py

Ros Build name: esp_serial

Published topic(s): None

Subscription topic(s): four_way_state, three_way_state,train_crossing_state,aux_state

Reference files: None

This is the bridge between ROS and the ESP interactive network. The code intakes the states above and concatenates the states into a single 16 index long integer array in the following order:

[four_way_state (1-4) ,three_way_state (1-4), train_crossing _state (1-4),aux_state(1-4)]

Then this array is broadcast via USB to all available ttyUSB devices listed at the time of activation, with utf-8 encoding.

This code can either be used for direct serial communication to endpoint nodes. Or via the ESP32 sender for wireless communications (highly recommended)

### Additional code files in package:

There are also code files for and from prior testing, they are included as bonus items, but not intended for core function, hence will only be lightly documented and function is not guaranteed.

Those files are:

- direct_master: interactive terminal designed to manually control lights, train ect ect. Prompts user.
- direct_light: A pared down version of direct master, for lights only
- direct_servo: a pared down of direct master for train crossing only
- testpub: broadcasts a series of test values to the four states received by esp_serial.

# Virtual Space

## World_gen

This is the big package. The entire visualizer system for the track is located within, with exception for some common functions, and the map_transforms utilized for odometry.

Code File: four_way_marker.py

Ros Build name: four_way_marker

Published topic(s): fourway_(1,2,3,4)

Subscription topic(s): four_way_state, custom_poses, marker_loc

Reference files: light.stl, light_pose.txt

This code file functions as one of many bridges between the track control states, and RVIZ.

At it’s core, there are two core behaviors.

The first, is the combined substriptions to custom_poses and marker_loc. (see these packages for their core function)

The system also parses the assigned _pose.txt file to make corrections to the mesh. In practice this file should be left with 0 pose X,y,z and 0 quaternion angles. This is merely to adjust meshes who have poorly aligned coordinate systems.

Upon receiving the location poses via custom_poses, the system then parses the marker_loc subscription to look for any locations bearing the “fourway_1” through 4 tag, then searches for the correct zone, and location for that tag. And assigns the marker pose to the coordinates contained within.

The second utilizes the subscription to “four_way_state” . When receiving the integer control states, the system performs a conversion from state value, to RGB color via an internal table. Then publish the marker mesh along “fourway_1” through 4 to RVIZ for visualization.

Code File: three_way_marker.py

Ros Build name: three_way_marker

Published topic(s): threeway_(1,2,3,4)

Subscription topic(s): three_way_state, custom_poses, marker_loc

Reference files: light.stl, light_pose.txt

This code file functions as one of many bridges between the track control states, and RVIZ.

At it’s core, there are two core behaviors.

The first, is the combined subscriptions to custom_poses and marker_loc. (see these packages for their core function)

The system also parses the assigned _pose.txt file to make corrections to the mesh. In practice this file should be left with 0 pose X,y,z and 0 quaternion angles. This is merely to adjust meshes who have poorly aligned coordinate systems.

Upon receiving the location poses via custom_poses, the system then parses the marker_loc subscription to look for any locations bearing the “threeway_1” through 4 tag, then searches for the correct zone, and location for that tag. And assigns the marker pose to the coordinates contained within.

The second utilizes the subscription to “three_way_state” . When receiving the integer control states, the system performs a conversion from state value, to RGB color via an internal table. Then publish the marker mesh along “train_1” through 4 to RVIZ for visualization.

Code File: train_marker.py

Ros Build name: train_marker

Published topic(s): train_(1,2,3,4)

Subscription topic(s): train_crossing_state, custom_poses, marker_loc

Reference files: train_barrier.dae,train_barrier_pose.txt

This code file functions as one of many bridges between the track control states, and RVIZ.

At it’s core, there are two core behaviors.

The first, is the combined subscriptions to custom_poses and marker_loc. (see these packages for their core function)

Upon receiving the location poses via custom_poses, the system then parses the marker_loc subscription to look for any locations bearing the “threeway_1” through 4 tag, then searches for the correct zone, and location for that tag. And assigns the marker pose to the coordinates contained within.

The system also parses the assigned _pose.txt file to make corrections to the mesh. In practice this file should be left with 0 pose X,y,z and 0 quaternion angles. This is merely to adjust meshes who have poorly aligned coordinate systems.

The final piece utilizes the trainc_crossing_state subscription. The states within correspond to a Y axis angle rotation, which represents the barrier’s present angle. To work with this, the system adds this angle, to the 3 Euler angles contained within the custom_poses data. Then transforms to a quaternion for ROS publishing, over the train_1 through 4 topics.

Code File: stop_sign.py

Ros Build name: stop_sign

Published topic(s): stop_(1,2,3,4)

Subscription topic(s): custom_poses, marker_loc

Reference files: stop.dae,stop_pose.txt

This code file functions as one of many bridges between the track control states, and RVIZ.

At it’s core, there are two core behaviors.

The first, is the combined subscriptions to custom_poses and marker_loc. (see these packages for their core function)

Upon receiving the location poses via custom_poses, the system then parses the marker_loc subscription to look for any locations bearing the “stop_1” through 4 tag, then searches for the correct zone, and location for that tag. And assigns the marker pose to the coordinates contained within.

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

After determining the proper coordinates, the system then publishes a marker over the stop_1 through 4 topics to RVIZ.

Code File: yield_sign.py

Ros Build name: yield_sign

Published topic(s): yield_(1,2,3,4)

Subscription topic(s): custom_poses, marker_loc

Reference files: yield.dae,yield_pose.txt

See stop_sign above, function is identical

Code File: dragon.py

Ros Build name: dragon

Published topic(s): dragon_(1,2,3,4)

Subscription topic(s): custom_poses, marker_loc

Reference files: dragon.dae,dragon_pose.txt

See stop_sign above, function is identical

## Map_transforms

Code File: odom_to_map_key.py

Ros Build name: odom_to_map_key

Published topic(s): startbox_1, startbox_2,car_mesh_1, car_mesh_2

Subscription topic(s): odom, reset_car,custom_poses,marker_loc

Reference files: None

This file is one of the key bridges between real and virtual space.

At it’s core, there are two functions. One is to parse the custom poses and marker locations to determine the starting location of the vehicle. (Note, when first loaded, the vehicle will load to whatever it’s internal Pose is, Reset must be activated to move this). With this determined, a startbox mesh is published to that location.

The second is the node listens to the odometry data from the car with a 0.5 second frame buffer, strips out the pose data. Transforms this data from the base_link reference used, to the map reference needed. Then stores this pose data.

When Reset_Car is activated, the system captures the car’s current pose at the activation time, and saves this. Then subtracts this from the cars odom position. Adds the startbox location, then publishes this to the world as a simple mesh along car_mesh_1.

# Other

## Testing_pubs

## Custom_msgs

## X_core2

Note: there are a handful of other files inside the xcore2 package, such as pose_strip and formulas. These files are not directly run by any nodes, but contain techniques and formulas used by nearly all other files.

Code File: parse_and_pass.py

Ros Build name: pub_All_pose

Published topic(s): marker_loc,custom_poses

Subscription topic(s): none

Reference files: [world]_markers.txt, [world]_marker_loc.txt

This is the core of the virtual system. As the name implies, this code file parses the text files, and passes the data along topics to other nodes.

The first file contains the respective locations of all possible marker locations in the selected track. In the structure

[Index, Zone, Subzone, Extra, X,Y,Z position, X,Y,Z,W angles]

Note that currently the system is capable of passing quaternions, but all current subscription nodes utilize Euler angles in Radians.

Shown below is an example of that file, should any other locations be desired, simply add more coordinate points, with a zone and subzone. At this present, the Extra is currently unused.


The second file is used to assign the desired markers to the zones. In the structure:

[Node Name, Zone, Subzone]

Where the node name, due to how the system is structured, is also the marker’s published topic. The number at the end indicates which of the markers is being assigned to.

One example of this file is located below. To change the location a marker is assigned to, simply edit this file to change which marker is assigned to which location. Also, multiple markers can receive the same location. And simply disable them in RVIZ. Note that the names, zones, and subzones need to correspond EXACTLY to how they are listed in the file above, and the publisher topic names. Otherwise, the marker will appear at the origin.

Should this be a concern, run one of the individual marker publishers in a separate terminal, there are a series of print statements that will tell you what marker is going where, and if a zone or location can be found.


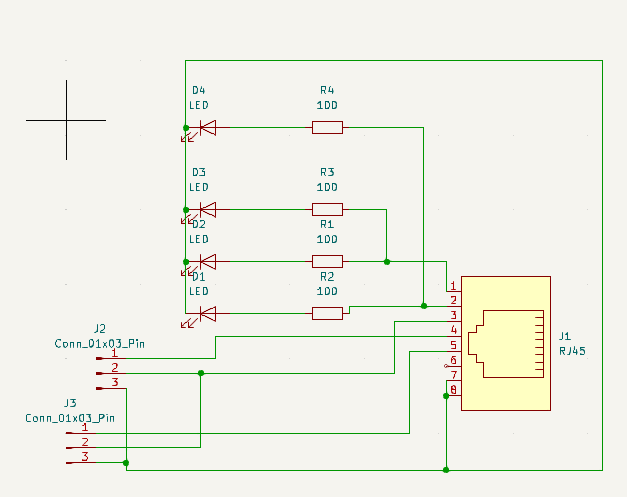
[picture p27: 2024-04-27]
InteractiveElements/Servo Adapter Pinout.png

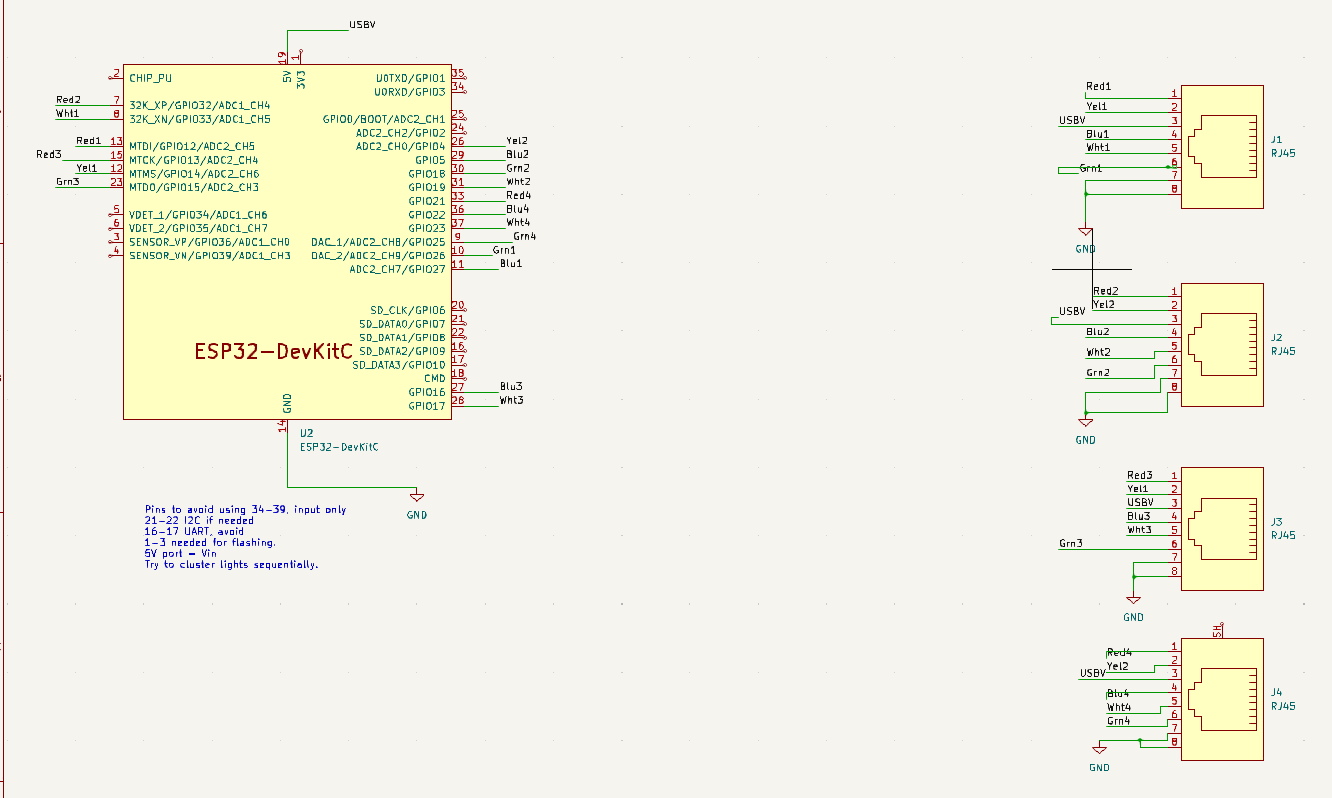
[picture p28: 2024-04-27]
InteractiveElements/Esp V2 Pinout.png

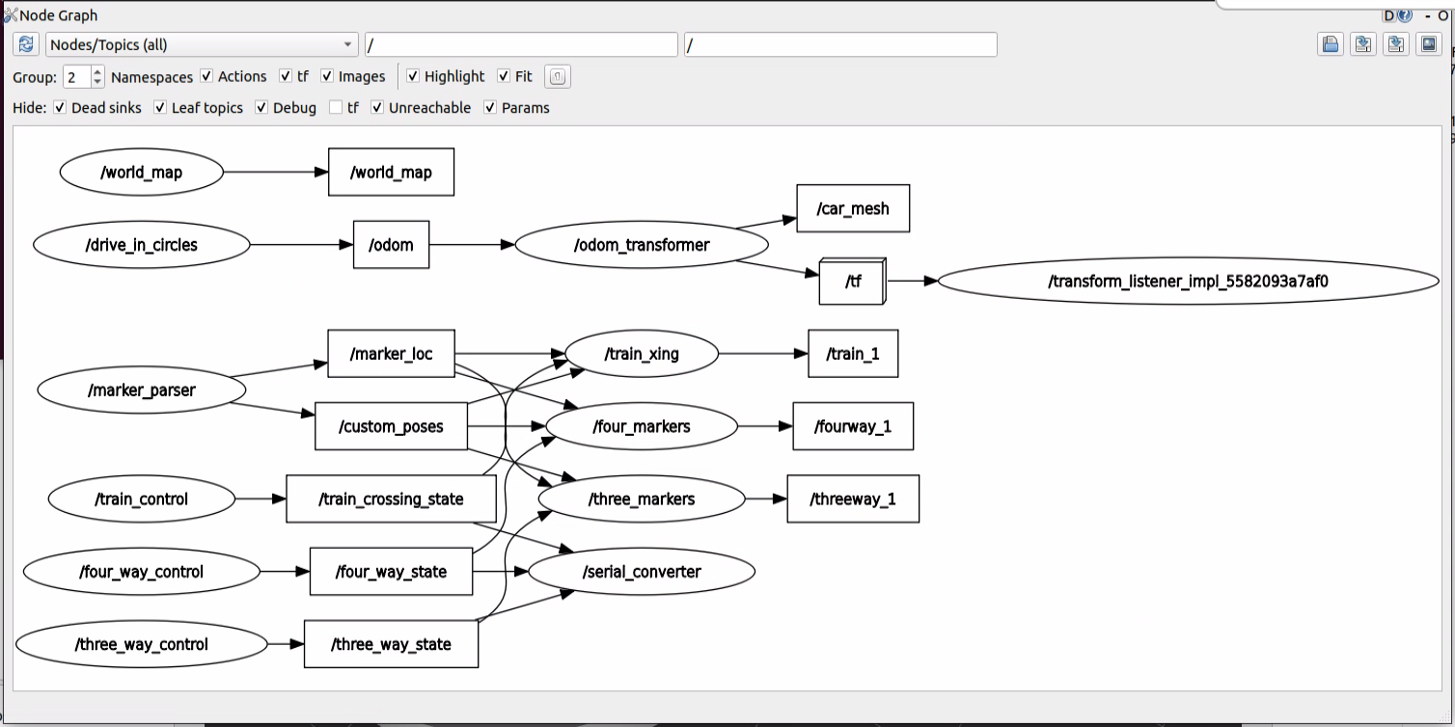
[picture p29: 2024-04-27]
Documentation/Images/System RQT.png

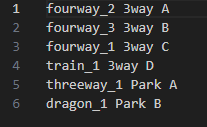
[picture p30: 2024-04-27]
Documentation/Images/World Marker...png

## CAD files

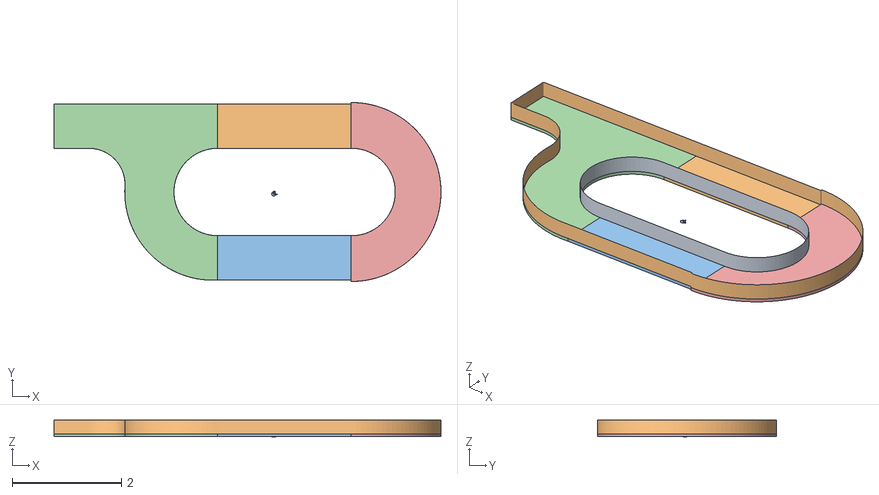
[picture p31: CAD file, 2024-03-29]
Mid Process Stuff/World Meshes/Full Oval Export Testing v2.obj
7.09 x 3.28 x 0.308

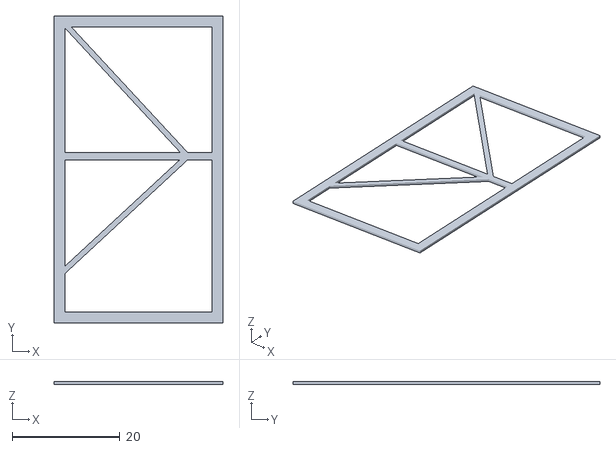
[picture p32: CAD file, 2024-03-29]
3D Modelling/Lights/Pattern 1 Main.stl
31.4 x 57.0 x 0.5

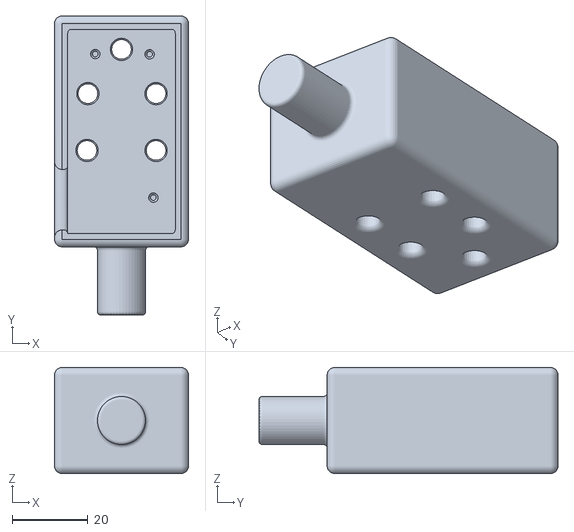
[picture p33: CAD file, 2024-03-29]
3D Modelling/Lights/Light Main Body.stl
35.4 x 79.0 x 28.0

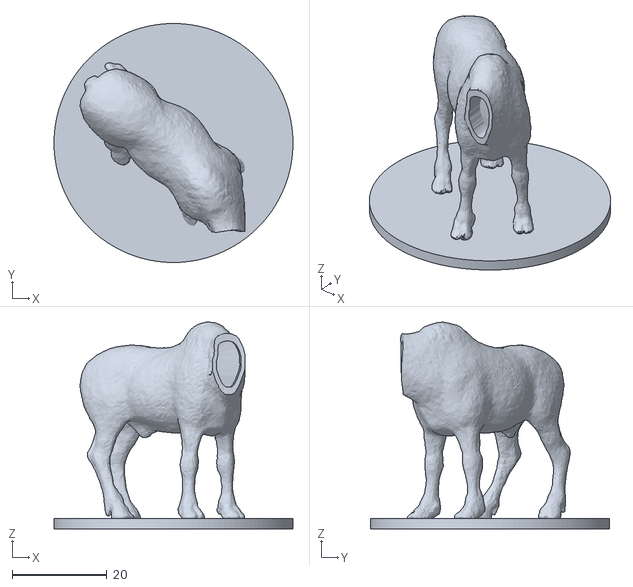
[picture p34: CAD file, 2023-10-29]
3D Modelling/Animal Models/Moose/moose_body.stl
50.5 x 50.5 x 43.7

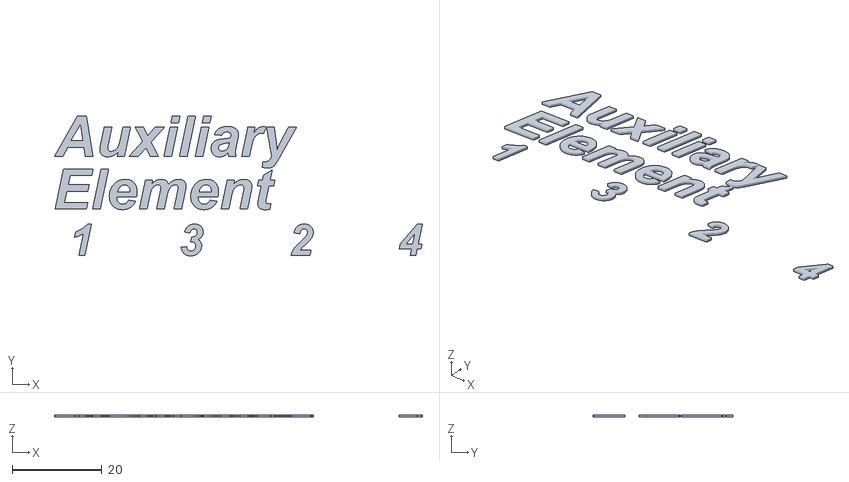
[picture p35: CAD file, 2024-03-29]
3D Modelling/Controller Boxes/ESP Control Boxes/Aux Label.stl
82.1 x 31.2 x 0.5

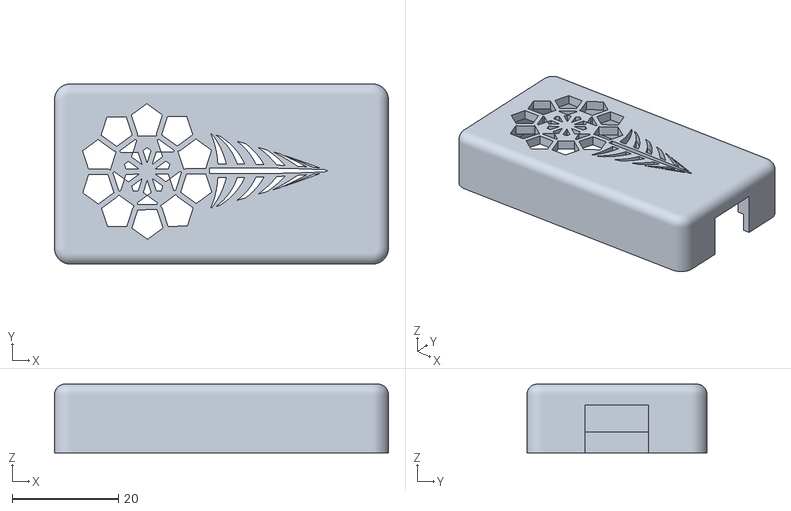
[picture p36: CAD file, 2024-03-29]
3D Modelling/Controller Boxes/ESP Transmitter Box/Esp lid with vent.stl
63.0 x 34.0 x 13.0

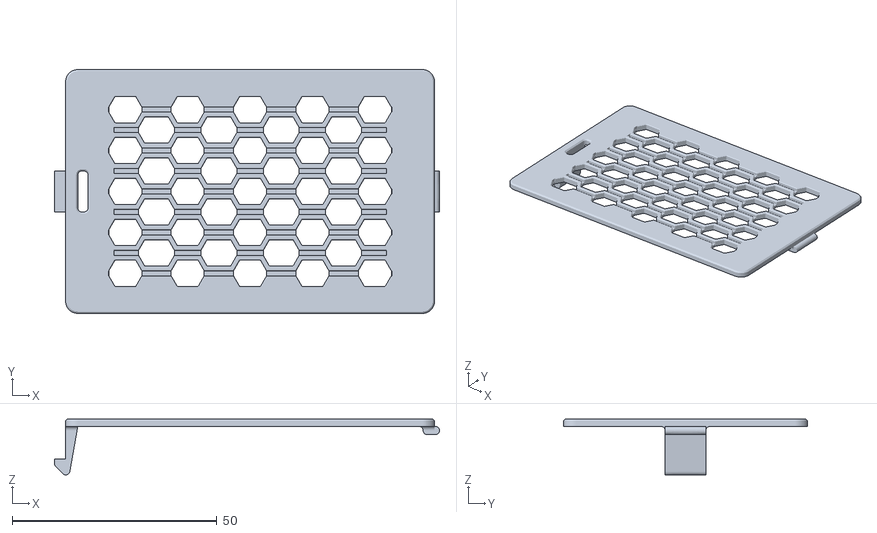
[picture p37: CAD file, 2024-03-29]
3D Modelling/Controller Boxes/Raspberry Pi Case/rpi-4-case-cover-hex.stl
94.1 x 59.6 x 13.7

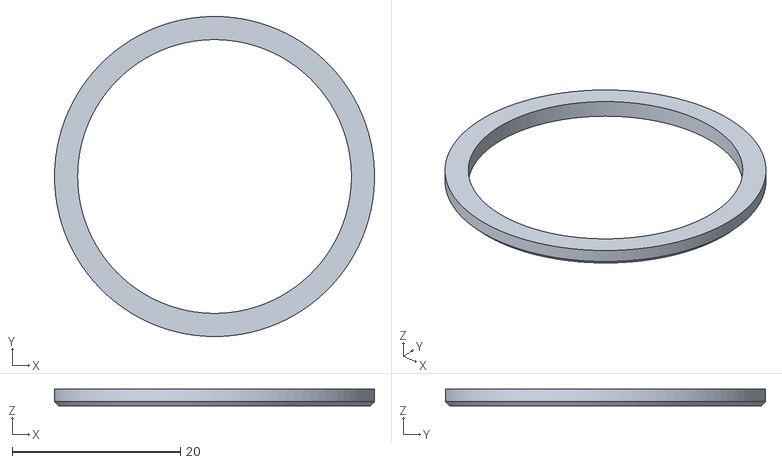
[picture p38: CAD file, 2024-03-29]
3D Modelling/Lidar Barrier Stuff/Individual STL's/Single Pole Color Ring.stl
38.0 x 38.0 x 2.00

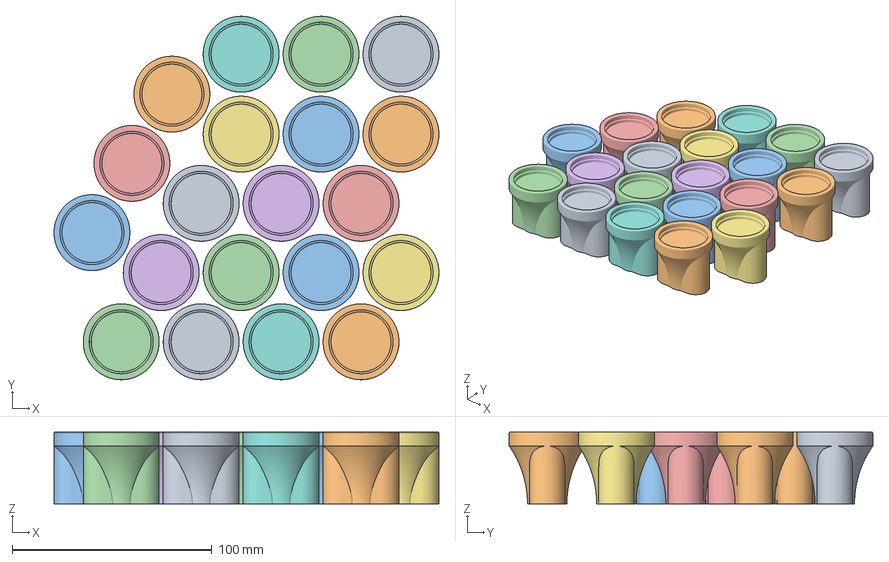
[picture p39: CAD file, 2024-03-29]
3D Modelling/Lidar Barrier Stuff/Print Plates for production/Double pole V2 20.3mf
192.6 x 181.9 x 36.0 mm
Spaced Double HD Solid.stl x 20

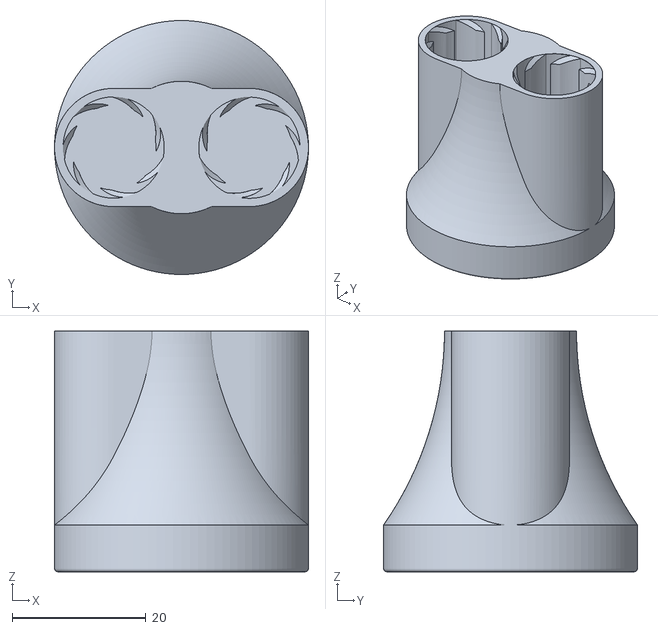
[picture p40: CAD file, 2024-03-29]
3D Modelling/Lidar Barrier Stuff/Spaced Double HD Solid.stl
38.0 x 38.0 x 36.0

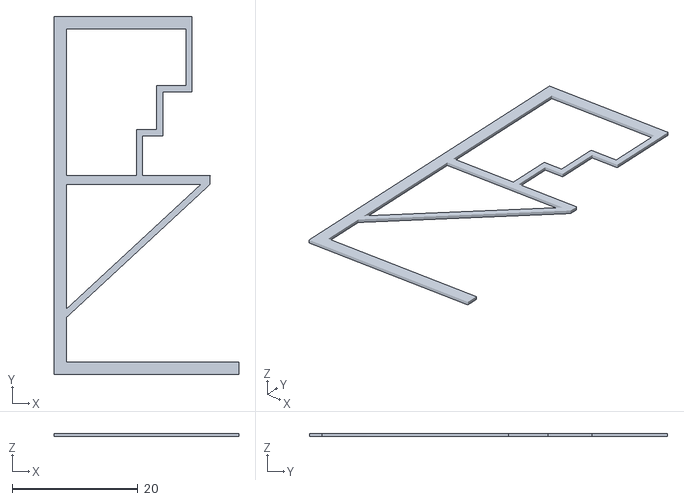
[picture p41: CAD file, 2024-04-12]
3D Modelling/Lights/Pattern 4.stl
29.4 x 57.0 x 0.5

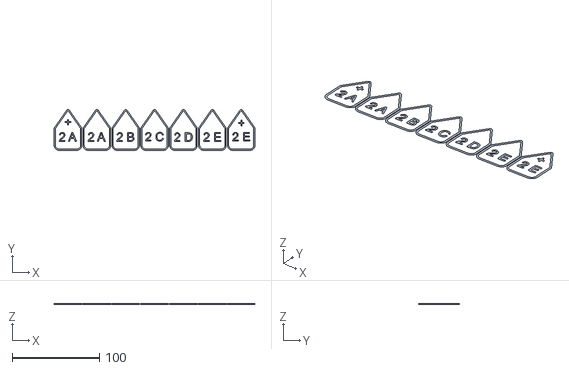
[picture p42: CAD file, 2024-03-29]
3D Modelling/Marker Chips/Arrow Markers/Arrow Letters2.stl
229.8 x 46.8 x 0.5

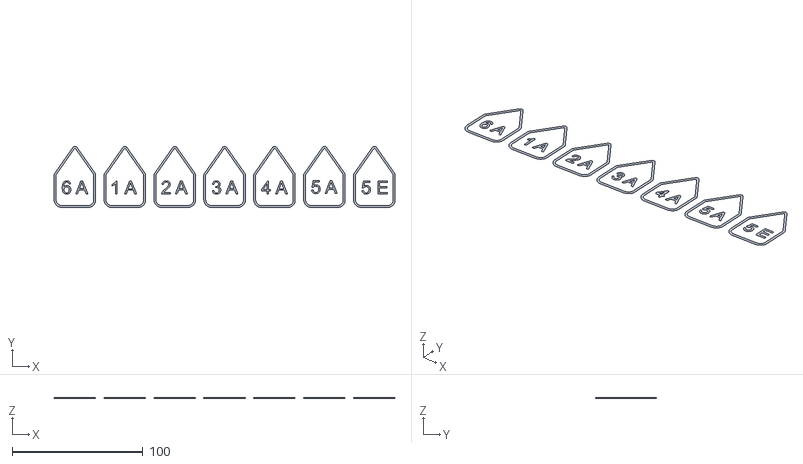
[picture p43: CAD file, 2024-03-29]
3D Modelling/Marker Chips/Blackout Markers/1-5.stl
260.3 x 46.8 x 0.5

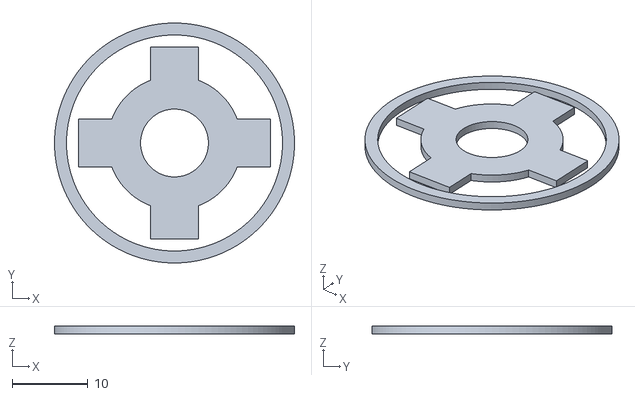
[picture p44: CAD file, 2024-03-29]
3D Modelling/Marker Chips/Roundabout Top.stl
31.8 x 31.7 x 1.00

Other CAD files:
3D Modelling/Marker Chips/Section Markers/Roundabout .75.stl
3D Modelling/Signs/Sign Holders.3mf
3D Modelling/Tools and Jigs/Pencil Sharpener v1.stl
3D Modelling/Train Crossing/Servo Holder new.3mf
3D Modelling/Animal Models/Moose/moose.3mf
3D Modelling/Animal Models/Moose/moose_head.stl
3D Modelling/Controller Boxes/ESP Control Boxes/3 Way Label.stl
3D Modelling/Controller Boxes/ESP Control Boxes/4 Way Label.stl
3D Modelling/Controller Boxes/ESP Control Boxes/ESP 4 Port Body.stl
3D Modelling/Controller Boxes/ESP Control Boxes/ESP 4 Port Lid Vented.stl
3D Modelling/Controller Boxes/ESP Control Boxes/ESP 4 Port Lid.stl
3D Modelling/Controller Boxes/ESP Control Boxes/Train Crossing Label.stl
3D Modelling/Controller Boxes/ESP Transmitter Box/38 Pin ESP Pin Protector.stl
3D Modelling/Controller Boxes/ESP Transmitter Box/ESP 38 Pin base.stl
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

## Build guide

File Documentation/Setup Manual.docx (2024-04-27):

# Setup Manual

Project 25 – Responsive and Interactive Urban Track for Autonomous Vehicles

Team Members:

Date | Revision | Release Notes
1/14/2024 | 01 | Initial Release
4/27/24 | 02 | Final Release

# 1. Product Overview

This product is an interactive urban track with physical and virtual world components created for small-scale autonomous cars. This documentation provides information on the given equipment and hardware and software setup.

# 2. Product Features

This product includes multiple track layouts to test small-scale autonomous vehicles. The road features that are possible to encounter include a roundabout, a four way intersection, a three way intersection, and a passing lane. Not all of these road features are present on each track layout; within the Track Layout Configurations section there will be a list of what testing opportunities are available in each layout.

There are multiple interactive elements of the track that provide opportunities to test the vehicles as well. This includes stop lights, stop signs, yield signs, and a railroad crossing. The elements have specific locations that they should be placed at in order for the virtual world to match the physical world properly.

This product utilizes a free software package that creates a virtual world that is synchronized with the physical track. This virtual world displays the current track layout, interactive element locations, and the vehicle on the track.

# 3. Physical Track

## 3.1 Given Equipment

- Track Mats
- Barrier Fabric Pieces
- Single Pole Mounting Points
- Double Pole Mounting Points
- Interactive Elements
  - Stop Lights
  - Stop Signs
  - Yield Signs
  - 1 Railroad Crossing
- 1 Raspberry PI 4

## 3.2 Track Layout Configurations

There are 5 track layouts with full operability outlined in this document. These layouts come with different testing opportunities for the vehicles. They also vary in sizes between 12x38ft and 12x16ft.

All tracks are divided into individual columns (1-19) each with a fixed number of rows. Between the different setups the columns will change, so it is important to be aware of which columns are being used in each setup. Each setup has instructions for which numbered columns are to be used out of each section: entrance, straightaway, four-way, roundabout, semicircle.

### 3.2.1 Medium Four Way

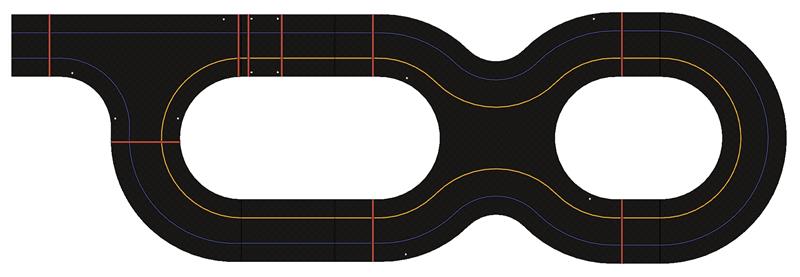
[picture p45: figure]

Track columns used:

Track Sections | Entrance | Straightaway | Four Way | Roundabout | Semicircle
Track Columns | 1-5 | 6-7 | 10-16 | X | 17-19

Functionality:

  - Four-way intersection
    - With stop lights
    - With stop signs
  - Three-way intersection
    - With stop lights
    - With stop signs
  - Passing lane
  - Railroad crossing

### 3.2.2 Small Four Way

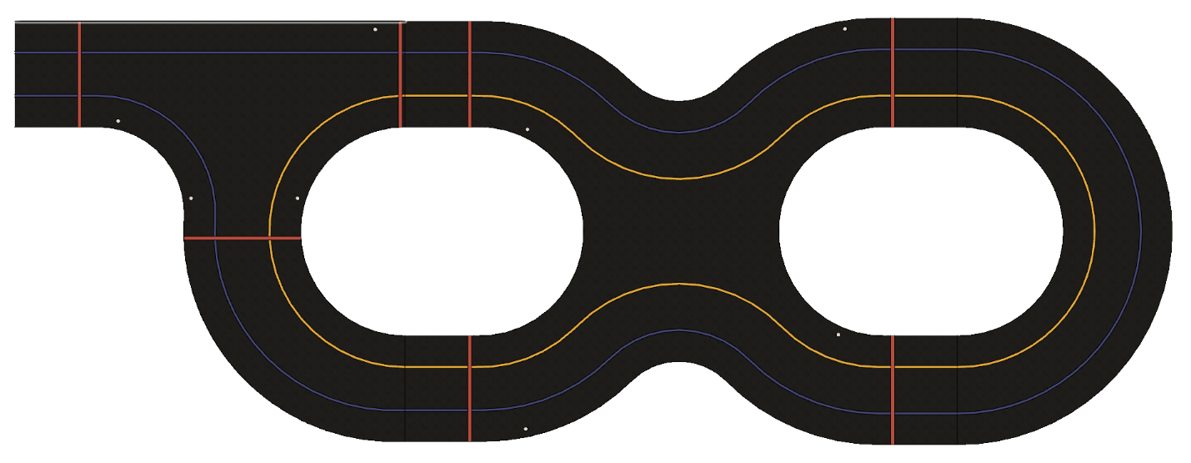
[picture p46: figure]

Track columns used:

Track Sections | Entrance | Straightaway | Four Way | Roundabout | Semicircle
Track Columns | 1-5 | X | 10-16 | X | 17-19

Functionality:

  - Four-way intersection
    - With stop lights
    - With stop signs
  - Three-way intersection
    - With stop lights
    - With stop signs
  - Passing lane
  - Railroad crossing

### 3.2.3 Medium Roundabout

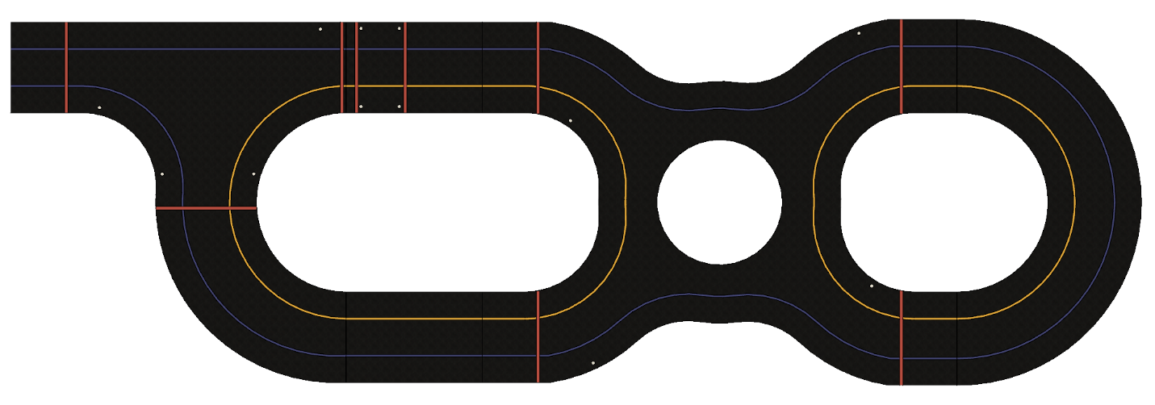
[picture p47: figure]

Track columns used:

Track Sections | Entrance | Straightaway | Four Way | Roundabout | Semicircle
Track Columns | 1-5 | 6-7 | X | 10-16 | 17-19

Functionality:

  - Roundabout
    - With yield signs
  - Three-way intersection
    - With stop lights
    - With stop signs
  - Passing lane
  - Railroad crossing

### Small Roundabout

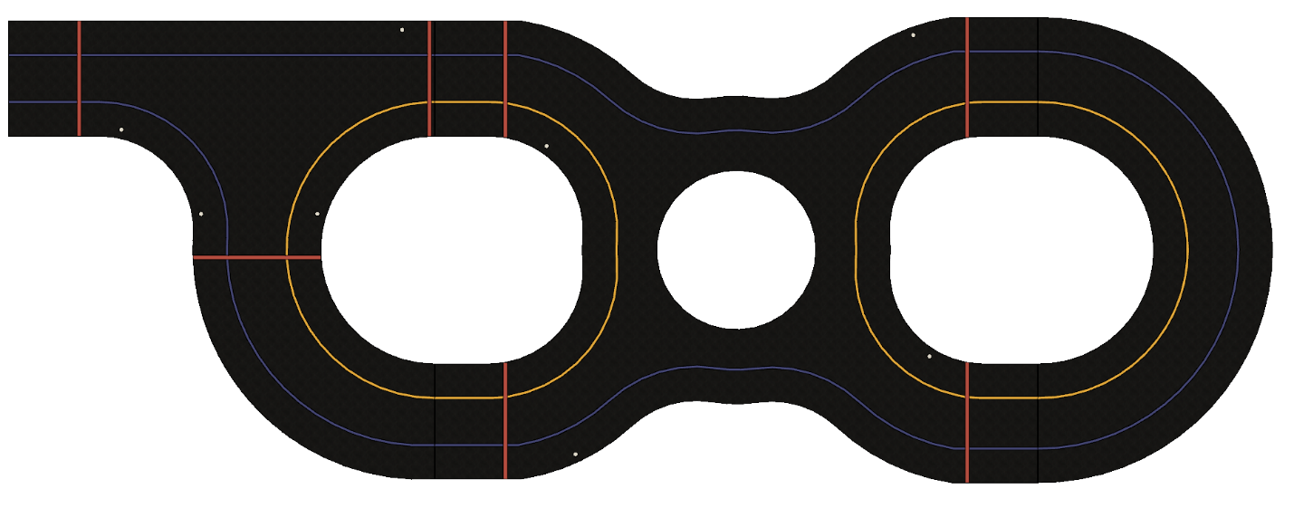
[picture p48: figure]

Track columns used:

Track Sections | Entrance | Straightaway | Four Way | Roundabout | Semicircle
Track Columns | 1-5 | X | X | 10-16 | 17-19

Functionality:

  - Roundabout
    - With yield signs
  - Three-way intersection
    - With stop lights
    - With stop signs
  - Passing lane
  - Railroad crossing

### 3.2.4 Full Oval

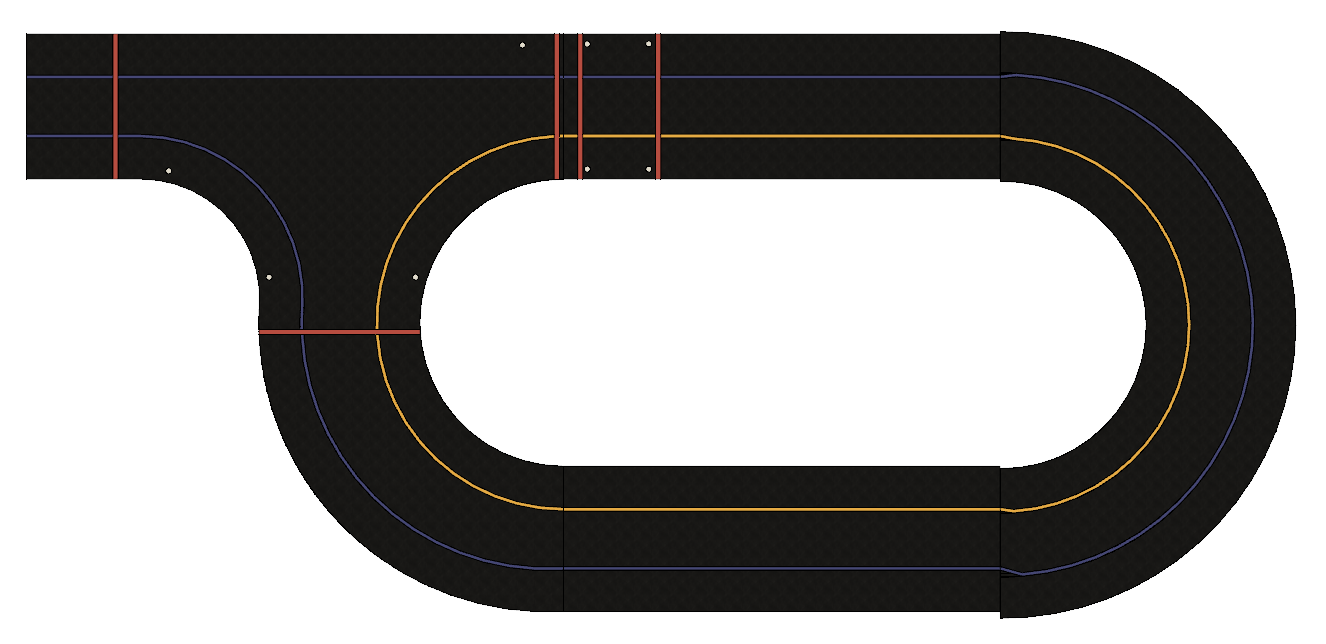
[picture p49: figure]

Track columns used:

Track Sections | Entrance | Straightaway | Four Way | Roundabout | Semicircle
Track Columns | 1-5 | 6-9 | X | X | 17-19

Functionality:

  - Three-way intersection
    - With stop lights
    - With stop signs
  - Passing lane
  - Railroad crossing

### 3.2.5 Medium Oval

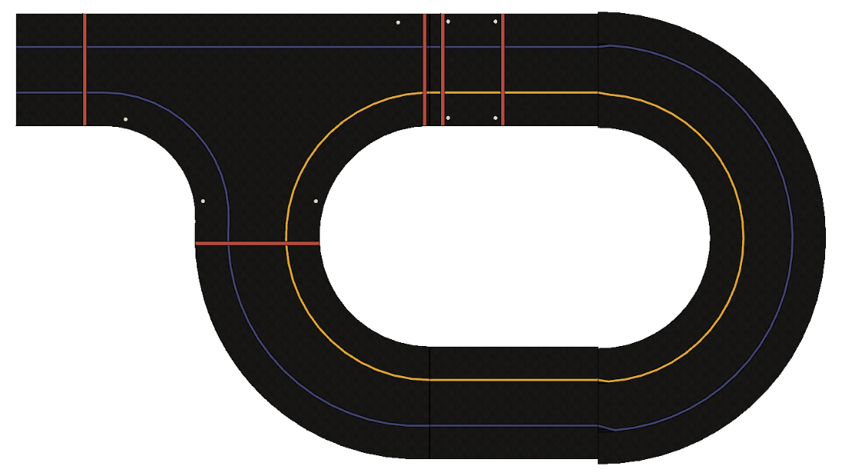
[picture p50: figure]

Track columns used:

Track Sections | Entrance | Straightaway | Four Way | Roundabout | Semicircle
Track Columns | 1-5 | 6-7 | X | X | 17-19

Functionality:

  - Three-way intersection
    - With stop lights
    - With stop signs
  - Passing lane
  - Railroad crossing

### 3.2.6 Small Oval

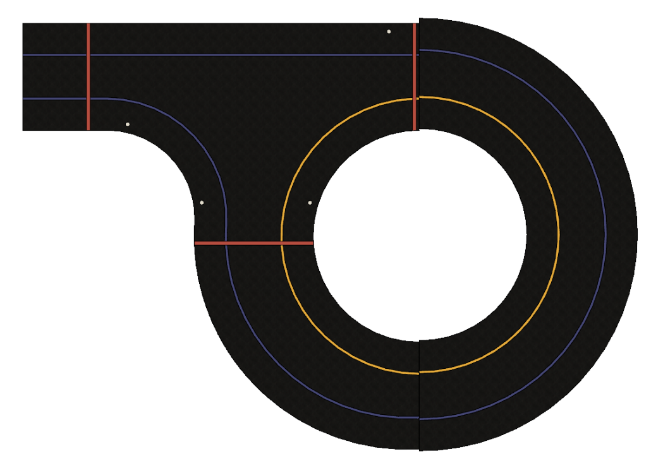
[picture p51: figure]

Track columns used:

Track Sections | Entrance | Straightaway | Four Way | Roundabout | Semicircle
Track Columns | 1-5 | X | X | X | 17-19

Functionality:

  - Three-way intersection
    - With stop lights
    - With stop signs

## 3.3 Barrier Configuration

Each barrier fabric piece is ~60 in long with a few smaller options for filling in smaller gaps. These fabric pieces are slid onto wooden dowels of a length of about 9 in. Then, the dowels are attached to mounting points that are either for one or two poles. The single and double mounting points can be seen below in Figure 1.

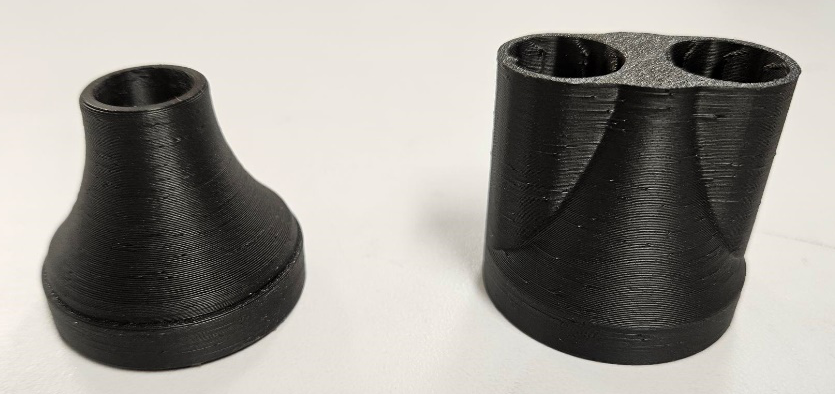
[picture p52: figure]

Figure 1: Single and Double Mounting Points

Dowels attached to a single mounting point do not have attached fabric pieces; dowels attached to a double mounting point have attached fabric pieces. On average, there are about 5 single mounting points between two double mounting points, though 4 should be assumed when setting up so as to save time if the fabric cannot reach. A complete setup barrier is shown in Figure 2.

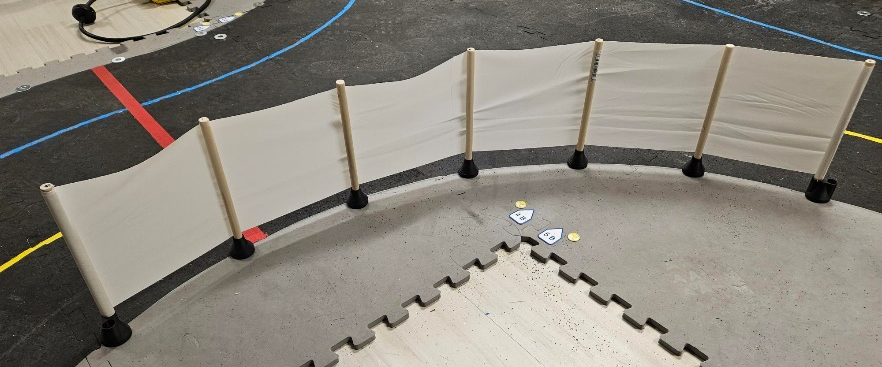
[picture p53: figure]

Figure 2: Barrier Example

Put enough barriers around the edges of the track to ensure the car cannot escape.

## 3.4 Interactive Element Configuration

### 3.4.1 Stop Sign

The stop sign interactive elements are assembled using the one tenth scale stop signs as well as one single mounting point. The post attached to the stop sign fits snugly into the single mounting point and can be rotated to the desired angle. The stop signs can be implemented at all mounting points in the entrance, roundabout, and four-way section.

### 3.4.2 Yield Sign

Similar to the stop sign, the yield sign interactive elements are assembled using the one tenth scale yield sign as well as a single mounting point. The post attached to the yield sign fits snugly into the single mounting point and can be rotated to the desired angle. The yield signs can be implemented at all mounting points in the entrance, roundabout, and four-way section.

### 3.4.3 Stop Lights

The stop light interactive elements are assembled with an ESP32 receiver, LEDs, as well as one single mounting point. The post attached to the stop light fits snugly into the single mounting point and can be rotated to the desired angle. The stop lights can be implemented at all mounting points in the entrance and four-way section.

### 3.4.4 Railroad Crossing

The railroad crossing interactive element works with a servo motor and an ESP32 receiver. Each side of the crossing is attached to one single mounting point. The crossing can only be implemented on the straightaway section of the track.

# 4. Software Implementation

This track requires multiple software products to run as intended.

## 4.1 Software Products

In order to run the track, the following software products in Table 1 are required. This table also includes links to download the products.

Table 1: Required Software to Run Track

Software Product | Website to download
ROS Humble Desktop Package | https://docs.ros.org/en/humble/Installation/Ubuntu-Install-Debians.html
NoMachine | https://www.nomachine.com/
VS Code | https://code.visualstudio.com/
Linux 22.04 | https://releases.ubuntu.com/jammy/
Docker | https://docs.docker.com/get-docker/
Core Files | https://github.com/UVMAirLabTrack/Track23

## 4.2 Launch Files

All contained under the world_gen package.

all_viewer_launch: This boots up the visualizer node, with all marker types enabled. Including the stoplights, signs, train crossing, and dragon. Also boots up the odom_to_map_key executable to transform the car odometry to the map. And the Gen_v2 to create the world mesh

Within, the various labelled publishers will display status messages.

Packages utilized:

• World_gen: Four_Way_marker

• World_gen: Three_Way_marker

• World_gen: Stop_sign

• World_gen: Yield_Sign

• World_gen: Train_marker

• Map_transforms: Odom_to_map_key

• World_gen: Gen_v2

• Xcore2: pub_All_pose

Track_launch: Loads up the three_way, four_way and train control signal publishers, As well as the ESP_serial node, which performs serial to wireless communications. This file is intended to be run on the Pi, or whatever computer you are utilizing to connect to the ESP network. Published state messages are shown in the terminal window.

Packages utilized:

• Four_way_light: gen

• three_way_light: gen

• train_crossing: gen

• direct_io: esp_serial

Train_viewer_launch: Similar to All_viewer_launch, except only the train crossing markers are loaded.

Light_viewer_launch: similar to all_viewer_launch, except only the 3 and 4 way lights are loaded.

At present, all viewer launch files utilize the same RVIZ configuration file, in the future it is suggested to build thinner and lighter versions for each configuration.

## 4.3 Interactive Controls

### 4.3.1 Four_way_light

Code File: pub.py

Ros Build name: pub

Published topic(s): four_way_state

Subscription topic(s): None

Reference files: light_states_4.txt

This package contains a single core file, “pub”

The function is to parse the reference file of light states, and pass them along the topic in the structure of a 4 integer array to control the stoplight in the real and virtual space.

That array looks like: [Light1, Light2, Light3, Light4]

At present only 4 states are utilized, with the rest existing for expansion.

They are:

• 0: All Lights Off

• 1: “Red” Uses a pattern of the Red, White, and Blue LED’s illuminated

• 2: “Yellow” Only the yellow LED is illuminated

• 3: “Green” The Green and Blue LED’s are illuminated

To change the light patterns: enter the CoreRaspberry/control folder, and edit “light_tates_4.txt” Opening the file will look something like the figure below:

The system takes the first 4 numbers in a row, and sets the control variables for the lights, publishes, then waits the number of seconds specified by the 5th number in the row. Then moves to the next line. Then cycles back to the first entry when the last is reached.

### 4.3.2 Three_way_light

Code File: pub.py

Ros Build name: pub

Published topic(s): three_way_state

Subscription topic(s): None

Reference files: light_states_3.txt

The function is to parse the reference file of light states, and pass them along the topic in the structure of a 4 integer array to control the stoplight in the real and virtual space.

That array looks like: [Light1, Light2, Light3, Light4]

At present only 4 states are utilized, with the rest existing for expansion.

They are:

- 0: All Lights Off
- 1: “Red” Uses a pattern of the Red, White, and Blue LED’s illuminated
- 2: “Yellow” Only the yellow LED is illuminated
- 3: “Green” The Green and Blue LED’s are illuminated

To change the light patterns: enter the CoreRaspberry/control folder, and edit “light_tates_3.txt” Opening the file will look something like the figure below:

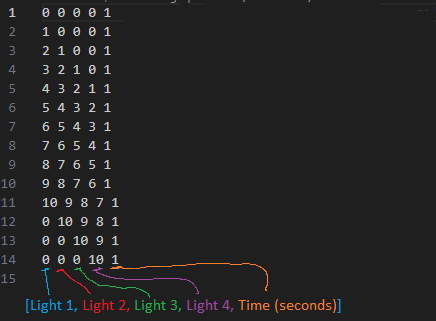
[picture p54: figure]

The system takes the first 4 numbers in a row, and sets the control variables for the lights, publishes, then waits the number of seconds specified by the 5th number in the row. Then moves to the next line. Then cycles back to the first entry when the last is reached.

### 4.3.3 Train_crossing

Code File: pub.py

Ros Build name: pub

Published topic(s): train_crossing_state

Subscription topic(s): None

Reference files: train_states.txt

The function is to parse the reference file of crossing states, and pass them along the topic in the structure of a 4 integer array to control the barrier in the real and virtual space.

That array looks like: [Barrier1, Barrier2, Barrier3, Barrier4]

Each barrier state refers to an angle in degrees. With 0 being down, angles up to 180 are possible, but will likely run into obstruction by the fabric “Lidar fence”.

To change the barrier patterns: enter the CoreRaspberry/control folder, and edit “train_states.txt” Opening the file will look something like the figure below:

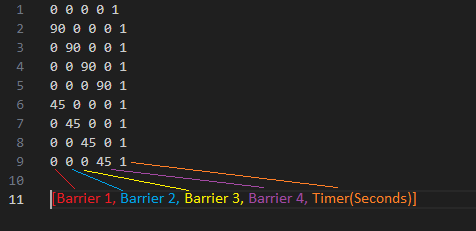
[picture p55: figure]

The system takes the first 4 numbers in a row, and sets the control variables for the barriers, publishes, then waits the number of seconds specified by the 5th number in the row. Then moves to the next line. Then cycles back to the first entry when the last is reached.

### 4.3.4 Direct_io

Code File: esp_serial.py

Ros Build name: esp_serial

Published topic(s): None

Subscription topic(s): four_way_state, three_way_state,train_crossing_state,aux_state

Reference files: None

This is the bridge between ROS and the ESP interactive network. The code intakes the states above and concatenates the states into a single 16 index long integer array in the following order:

[four_way_state (1-4) ,three_way_state (1-4), train_crossing _state (1-4),aux_state(1-4)]

Then this array is broadcast via USB to all available ttyUSB devices listed at the time of activation, with utf-8 encoding.

This code can either be used for direct serial communication to endpoint nodes. Or via the ESP32 sender for wireless communications (highly recommended)

#### Additional code files in package:

There are also code files for and from prior testing, they are included as bonus items, but not intended for core function, hence will only be lightly documented and function is not guaranteed.

Those files are:

- direct_master: interactive terminal designed to manually control lights, train ect ect. Prompts user.
- direct_light: A pared down version of direct master, for lights only
- direct_servo: a pared down of direct master for train crossing only
- testpub: broadcasts a series of test values to the four states received by esp_serial.

## 4.4 Virtual Space

### 4.4.1 World Gen

This is the big package. The entire visualizer system for the track is located within, with exception for some common functions, and the map_transforms utilized for odometry.

Code File: four_way_marker.py

Ros Build name: four_way_marker

Published topic(s): fourway_(1,2,3,4)

Subscription topic(s): four_way_state, custom_poses, marker_loc

Reference files: light.stl, light_pose.txt

This code file functions as one of many bridges between the track control states, and RVIZ.

At it’s core, there are two core behaviors.

The first, is the combined substriptions to custom_poses and marker_loc. (see these packages for their core function)

The system also parses the assigned _pose.txt file to make corrections to the mesh. In practice this file should be left with 0 pose X,y,z and 0 quaternion angles. This is merely to adjust meshes who have poorly aligned coordinate systems.

Upon receiving the location poses via custom_poses, the system then parses the marker_loc subscription to look for any locations bearing the “fourway_1” through 4 tag, then searches for the correct zone, and location for that tag. And assigns the marker pose to the coordinates contained within.

The second utilizes the subscription to “four_way_state” . When receiving the integer control states, the system performs a conversion from state value, to RGB color via an internal table. Then publish the marker mesh along “fourway_1” through 4 to RVIZ for visualization.

Code File: three_way_marker.py

Ros Build name: three_way_marker

Published topic(s): threeway_(1,2,3,4)

Subscription topic(s): three_way_state, custom_poses, marker_loc

Reference files: light.stl, light_pose.txt

This code file functions as one of many bridges between the track control states, and RVIZ.

At it’s core, there are two core behaviors.

The first, is the combined subscriptions to custom_poses and marker_loc. (see these packages for their core function)

The system also parses the assigned _pose.txt file to make corrections to the mesh. In practice this file should be left with 0 pose X,y,z and 0 quaternion angles. This is merely to adjust meshes who have poorly aligned coordinate systems.

Upon receiving the location poses via custom_poses, the system then parses the marker_loc subscription to look for any locations bearing the “threeway_1” through 4 tag, then searches for the correct zone, and location for that tag. And assigns the marker pose to the coordinates contained within.

The second utilizes the subscription to “three_way_state” . When receiving the integer control states, the system performs a conversion from state value, to RGB color via an internal table. Then publish the marker mesh along “train_1” through 4 to RVIZ for visualization.

Code File: train_marker.py

Ros Build name: train_marker

Published topic(s): train_(1,2,3,4)

Subscription topic(s): train_crossing_state, custom_poses, marker_loc

Reference files: train_barrier.dae,train_barrier_pose.txt

This code file functions as one of many bridges between the track control states, and RVIZ.

At it’s core, there are two core behaviors.

The first, is the combined subscriptions to custom_poses and marker_loc. (see these packages for their core function)

Upon receiving the location poses via custom_poses, the system then parses the marker_loc subscription to look for any locations bearing the “threeway_1” through 4 tag, then searches for the correct zone, and location for that tag. And assigns the marker pose to the coordinates contained within.

The system also parses the assigned _pose.txt file to make corrections to the mesh. In practice this file should be left with 0 pose X,y,z and 0 quaternion angles. This is merely to adjust meshes who have poorly aligned coordinate systems.

The final piece utilizes the trainc_crossing_state subscription. The states within correspond to a Y axis angle rotation, which represents the barrier’s present angle. To work with this, the system adds this angle, to the 3 Euler angles contained within the custom_poses data. Then transforms to a quaternion for ROS publishing, over the train_1 through 4 topics.

Code File: stop_sign.py

Ros Build name: stop_sign

Published topic(s): stop_(1,2,3,4)

Subscription topic(s): custom_poses, marker_loc

Reference files: stop.dae,stop_pose.txt

This code file functions as one of many bridges between the track control states, and RVIZ.

At it’s core, there are two core behaviors.

The first, is the combined subscriptions to custom_poses and marker_loc. (see these packages for their core function)

Upon receiving the location poses via custom_poses, the system then parses the marker_loc subscription to look for any locations bearing the “stop_1” through 4 tag, then searches for the correct zone, and location for that tag. And assigns the marker pose to the coordinates contained within.

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

After determining the proper coordinates, the system then publishes a marker over the stop_1 through 4 topics to RVIZ.

Code File: yield_sign.py

Ros Build name: yield_sign

Published topic(s): yield_(1,2,3,4)

Subscription topic(s): custom_poses, marker_loc

Reference files: yield.dae,yield_pose.txt

See stop_sign above, function is identical

Code File: dragon.py

Ros Build name: dragon

Published topic(s): dragon_(1,2,3,4)

Subscription topic(s): custom_poses, marker_loc

Reference files: dragon.dae,dragon_pose.txt

See stop_sign above, function is identical

### 4.4.2 Map_transforms

Code File: odom_to_map_key.py

Ros Build name: odom_to_map_key

Published topic(s): startbox_1, startbox_2,car_mesh_1, car_mesh_2

Subscription topic(s): odom, reset_car,custom_poses,marker_loc

Reference files: None

This file is one of the key bridges between real and virtual space.

At it’s core, there are two functions. One is to parse the custom poses and marker locations to determine the starting location of the vehicle. (Note, when first loaded, the vehicle will load to whatever it’s internal Pose is, Reset must be activated to move this). With this determined, a startbox mesh is published to that location.

The second is the node listens to the odometry data from the car with a 0.5 second frame buffer, strips out the pose data. Transforms this data from the base_link reference used, to the map reference needed. Then stores this pose data.

When Reset_Car is activated, the system captures the car’s current pose at the activation time, and saves this. Then subtracts this from the cars odom position. Adds the startbox location, then publishes this to the world as a simple mesh along car_mesh_1.

## 4.5 Other

### 4.5.1 Custom_Messages

Code File: MarkerLoc.msg

Ros Build name: marker_loc

Published topic(s): N/A

Subscription topic(s): N/A

Reference files:N/A

Contains a simple code file used to create a new topic message structure used by other packages. See Image below for structure.

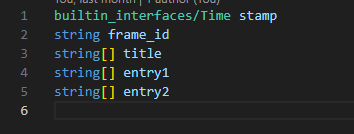
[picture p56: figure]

Code File: WorldMarkers.msg

Ros Build name: custom_poses

Published topic(s): N/A

Subscription topic(s): N/A

Reference files:N/A

Contains a simple code file used to create a new topic message structure used by other packages. See Image below for structure.

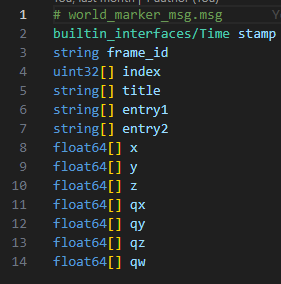
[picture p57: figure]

### 4.5.2 X_core2

Note: there are a handful of other files inside the xcore2 package, such as pose_strip and formulas. These files are not directly run by any nodes, but contain techniques and formulas used by nearly all other files.

Code File: parse_and_pass.py

Ros Build name: pub_All_pose

Published topic(s): marker_loc,custom_poses

Subscription topic(s): none

Reference files: [world]_markers.txt, [world]_marker_loc.txt

This is the core of the virtual system. As the name implies, this code file parses the text files, and passes the data along topics to other nodes.

The first file contains the respective locations of all possible marker locations in the selected track. In the structure

[Index, Zone, Subzone, Extra, X,Y,Z position, X,Y,Z,W angles]

Note that currently the system is capable of passing quaternions, but all current subscription nodes utilize Euler angles in Radians.

Shown below is an example of that file, should any other locations be desired, simply add more coordinate points, with a zone and subzone. At this present, the Extra is currently unused.

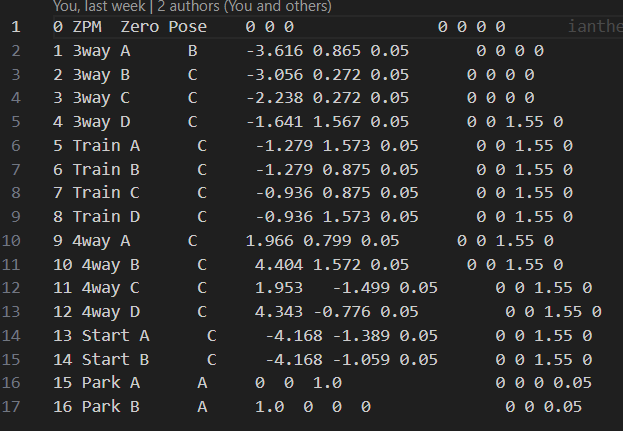
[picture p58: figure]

The second file is used to assign the desired markers to the zones. In the structure:

[Node Name, Zone, Subzone]

Where the node name, due to how the system is structured, is also the marker’s published topic. The number at the end indicates which of the markers is being assigned to.

One example of this file is located below. To change the location a marker is assigned to, simply edit this file to change which marker is assigned to which location. Also, multiple markers can receive the same location. And simply disable them in RVIZ. Note that the names, zones, and subzones need to correspond EXACTLY to how they are listed in the file above, and the publisher topic names. Otherwise, the marker will appear at the origin.

Should this be a concern, run one of the individual marker publishers in a separate terminal, there are a series of print statements that will tell you what marker is going where, and if a zone or location can be found.

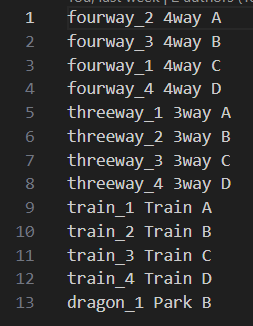
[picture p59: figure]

### 4.5.1 Marker mappings (not a code file)

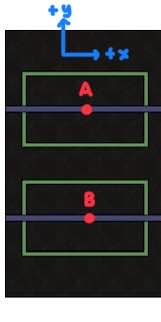
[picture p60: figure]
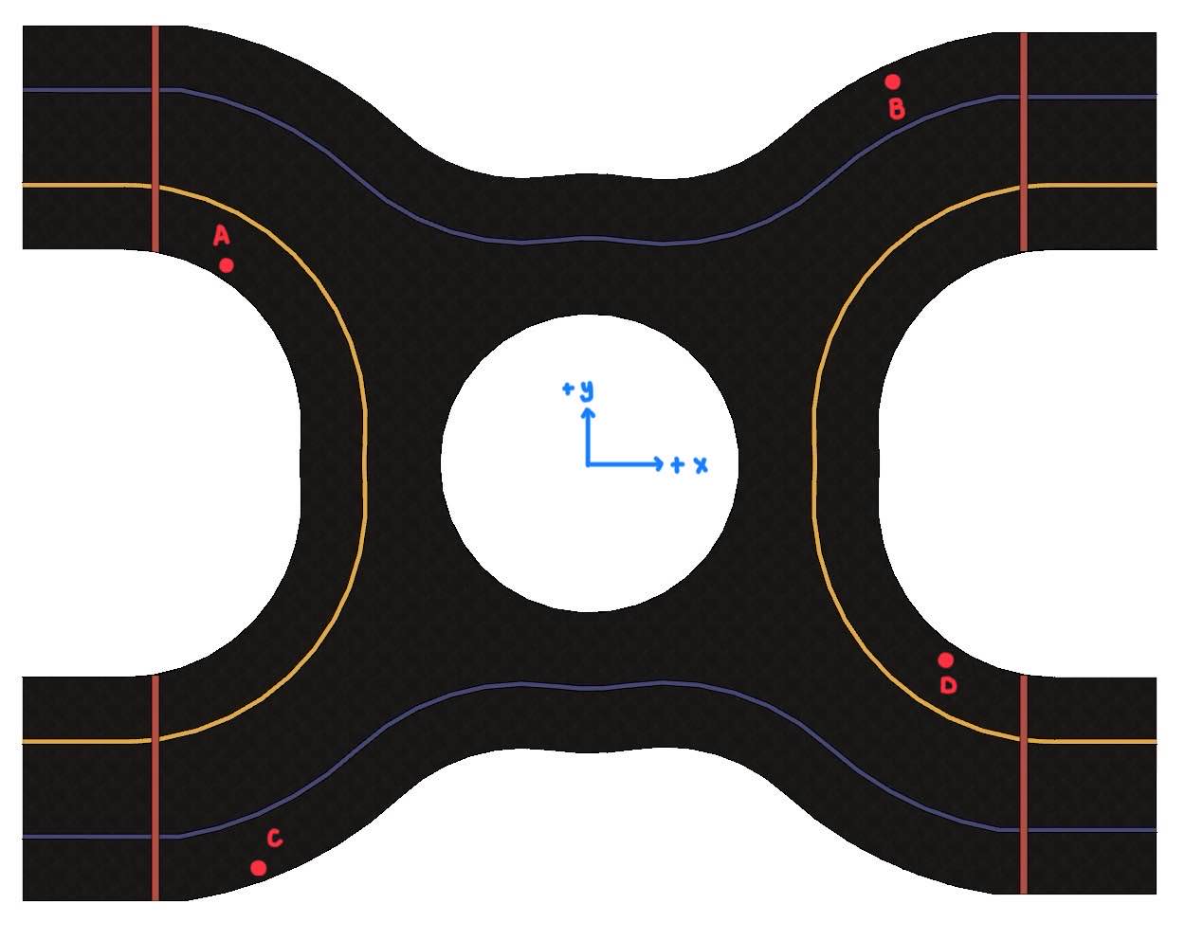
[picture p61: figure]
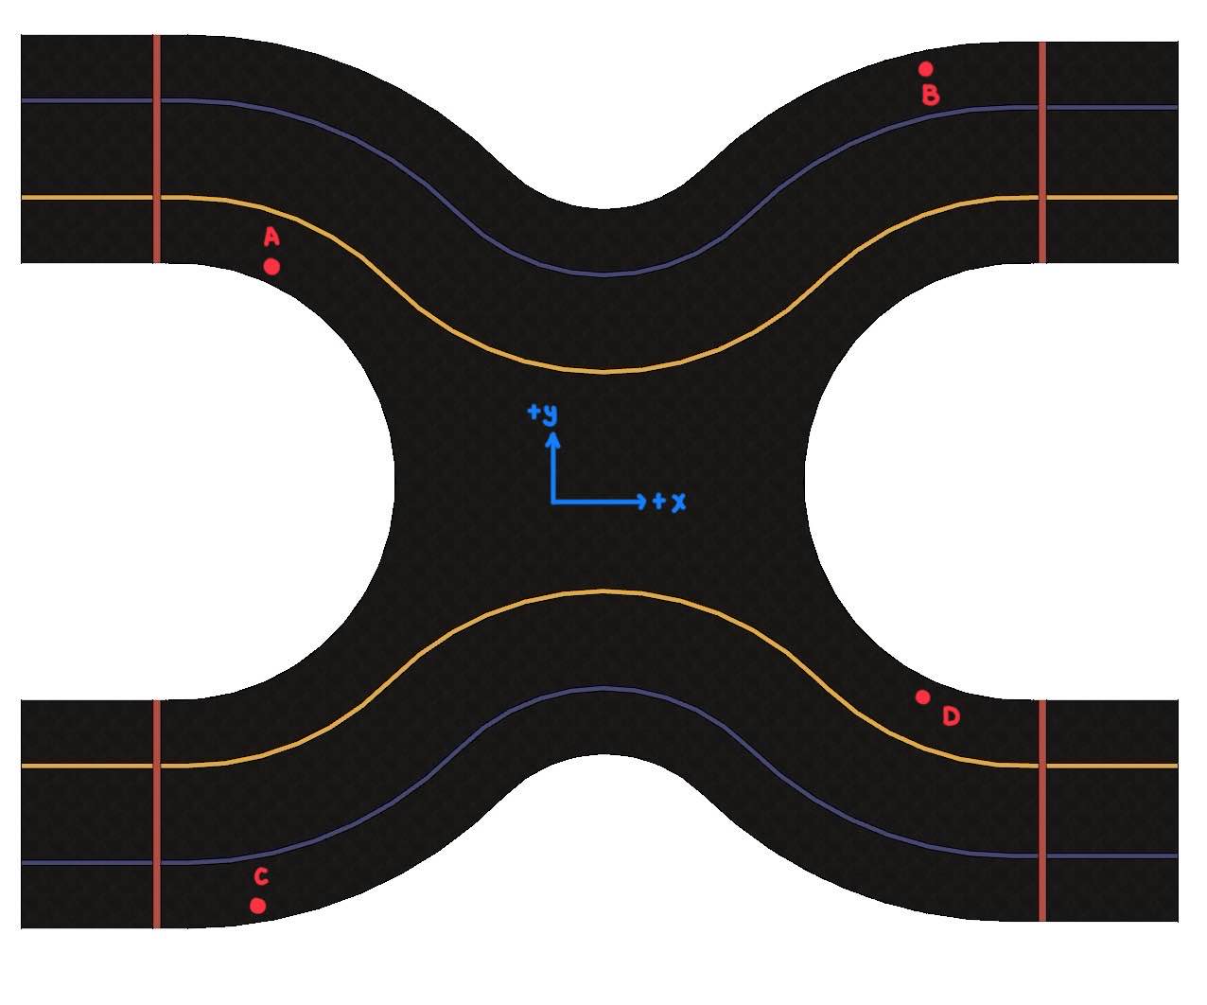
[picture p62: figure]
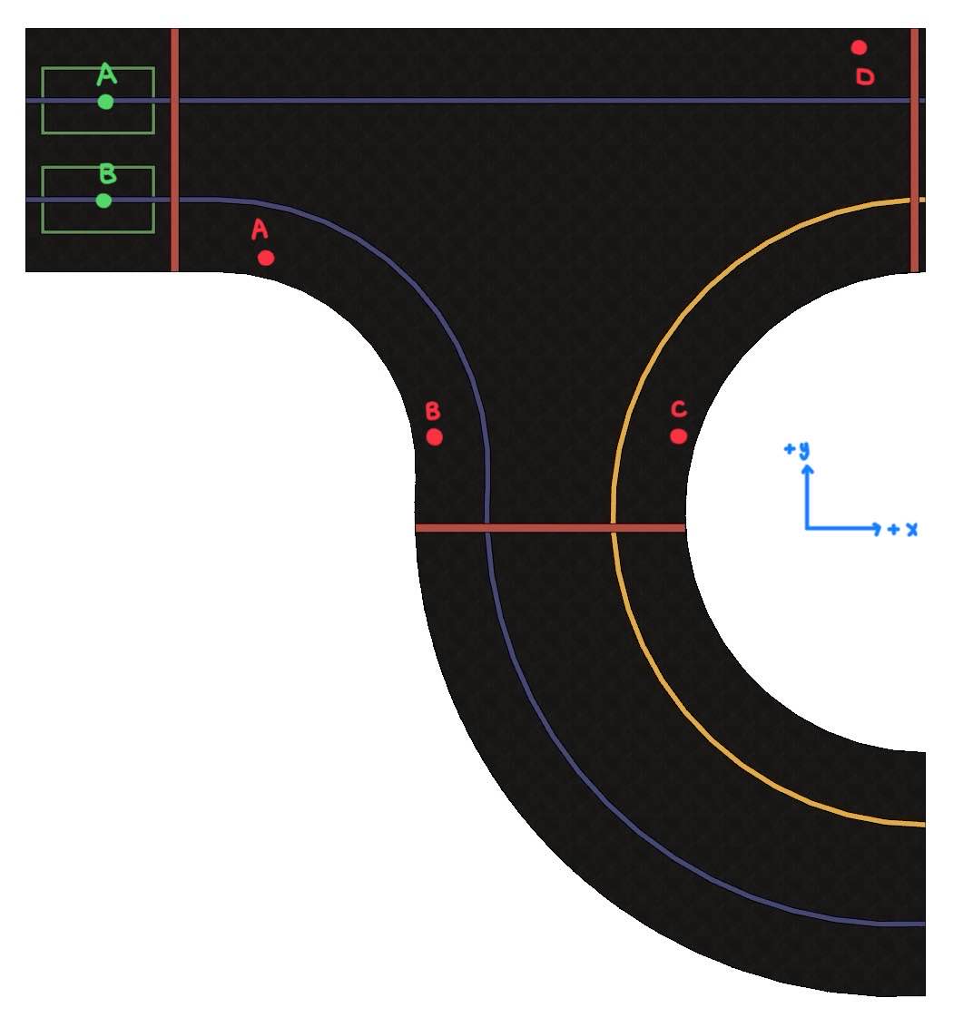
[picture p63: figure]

# 5. Example Setup

## 5.1 Example Physical Track Layout

For the example, the Medium Oval Track will be configured as it gives testing opportunities with four way intersections, as well as being the size of _____, which is not the largest the track can be. This allows for this example setup to be utilized by more places with varying size restraints.

## 5.2 Example Hardware Setup

1. Acquire the foam mats required for the entrance section (1-5) the medium straight aways (6-7), and the semicircle (17-19).

2. Assemble the Medium Oval Track layout

3. Erect single mounting points and dowels by attaching the black mounting point magnet to the washers and inserting the dowels into the points if not done so already. For every 4 single mounting points, a space should be left to allow for the double mounting points.

4. Place all double pointing points in the spaces left between every 4 single mounting points.

5. Insert the dowels attached to the barrier fabric into the double mounting points and spin the dowel to ensure that the barrier fabric is taught.

6. Place stop signs upon the four washer mounting points that exist within the entrance section.

7. Place the railroad crossing barriers upon the four washer mounting points that exist within the straight away section.

8. Attach a 10ft ethernet cable to the railroad crossing barrier and run the cord under the nearest seam of the foam mats. Bring the cord to the middle of the track where there are no foam mats and plug it into the raspberry pi. Repeat for every railroad crossing barrier, using a separate 10ft ethernet cable for each element.

## 5.3 Example Software Setup

To launch the example track. Open NoMachine from a computer connected to the same network as the Raspberry PI, and connect to “Track Pi” remotely.

Once inside, to launch the track nodes. Open a new terminal window. And run the command

Ros2 launch world_gen track_launch.py

This command will begin broadcasting commands to control the nodes on the track.

To launch the virtual space, (NOT ON THE PI!) load a linux environment with the software package for the track.

Navigate to RaspberryCore/CoreRaspberry/worlds. And edit the world_select.txt file.

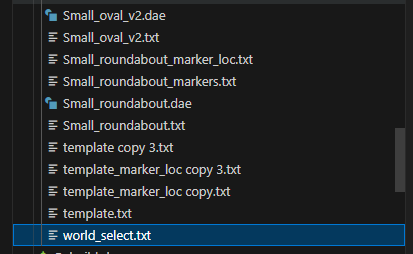
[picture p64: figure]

Once inside, place the “y” next to the “medium_oval” entry and save

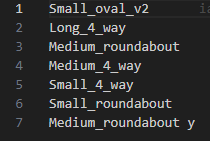
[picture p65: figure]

Next: open a terminal window and run the following command:

Ros2 launch world_gen all_viewer_launch.py

This will load RVIZ and the proper subscribers to view the world.

To add the car, and it’s odometry reset controller, run the following two commands in individual terminal windows.

Ros2 run map_transforms odom_to_map

Ros2 run map_transforms reset_car

A new Red mesh should appear in RVIZ now, to reset the car’s odometry to it’s “start box” open the reset_car terminal, and hit “Enter”

If for some reason communications are not established, it’s likely that the ros domain id is not correctly set. To fix this, add the following below, in front of the commands listed above

ROS_DOMAIN_ID=32 [command here]

# 6. Future Work

## 6.1 More Track Layouts

There is potential for two more tracks to be added with the following track columns:

Large Four Way

Track Sections | Entrance | Straightaway | Four Way | Roundabout | Semicircle
Track Columns | 1-5 | 6-7 | 10-16 | X | 17-19

Large Roundabout

Track Sections | Entrance | Straightaway | Four Way | Roundabout | Semicircle
Track Columns | 1-5 | 6-7 | X | 10-16 | 17-19

Project 25 Track Setup Manual 2

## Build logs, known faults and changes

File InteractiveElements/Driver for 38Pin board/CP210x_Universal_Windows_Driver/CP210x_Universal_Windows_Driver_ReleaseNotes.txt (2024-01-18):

RELEASE NOTES
=============
Silicon Labs Virtual COM Port (VCP) Universal Driver for Windows 10 version 1803 and later, windows 11

Package version: 11.3.0
Release date:    2023-05-26

This package contains a Virtual COM Port Universal driver for Microsoft
Windows 10 version 1803 and later, windows 11 versions of Windows for use with Silicon Labs VCP USB Serial Bridges.  These devices
include the CP2102N, CP2102, CP2103, CP2104, CP2105, CP2108, CP2109.

OS VERSIONS
-----------
This package provides the CP210x VCP driver for the following versions
of Windows:

- Windows 10 version 1803 and later (x64, x86)
- Windows 11    (x64)

CHOOSING VCP DRIVER VERSION
---------------------------
VCP drivers of version 11.1.0 and later are released for Microsoft
Windows 10 version 1803 and later, windows 11 versions of Windows as Universal Drivers.
This means they do not work on older version of Windows
such as Window 7 and 8.1.  You should use this driver if you only need
support for Windows 10 version 1803 and later, windows 11, or you need the Universal driver.  If you require
support on older versions of Windows, you should use the legacy VCP driver
which can be found on the Silicon Labs web site.  The legacy Windows VCP
drivers have version numbers less than 10.0.0.

CONTENTS
--------
The VCP driver package contains the following files and directories:
- silabser.inf -- Driver information file
- SLAB_License_Agreement_VCP_Windows.txt -- Software License
- CP210x_Universal_Windows_Driver_ReleaseNotes.txt -- this file

Additional files needed by installer
- silabser.cat
- x64/silabser.sys
- x86/silabser.sys

INSTALLING
----------
The VCP driver is automatically installed by Windows Update for CP210x with
alternate PID values of 0xEA63, 0xEA7A, and 0xEA7B.  These are not default
values.

Otherwise, unzip the .zip file and you will have a directory containing the
driver installer files.

### Prompted install ###

If Windows prompts you to install a driver for a CP210x device
(for example, if you plug a CP210x into your computer):

1. Use the dialog to browse for the driver location
2. Locate the driver folder (that you previously unzipped)
3. Follow the instructions

### Manual install ###

1. Using Windows File Explorer, locate the driver folder
   (that you previously unzipped)
2. Right click on the silabser.inf file and select Install
3. Follow the instructions

UNINSTALLING
------------
1. The device must be plugged in
2. Run Device Manager
3. Locate the device you want to uninstall
4. Right click on the device and choose "uninstall"
5. Follow the instructions

SETUP REGISTRY KEY
------------------
Registry keys are used for setting some parameters of the serial port
For setting these parameters, we have 2 ways:
	- Modify registry value using registry editor of Windows
	- Modify registry value using INF file
The detail of each method as following.
### Modify registry value using registry editor of Windows ###

1. Edit the file UpdateParameters.reg according to your settings, save the file.
   Registry keys are allocated at 3 position:
   - Parameters keys: HKEY_LOCAL_MACHINE\SYSTEM\CurrentControlSet\Services\silabser
   - Software keys:   HKEY_LOCAL_MACHINE\SYSTEM\CurrentControlSet\Control\Class\<ClassID>\
   - Hardware keys:   HKEY_LOCAL_MACHINE\SYSTEM\CurrentControlSet\Enum\USB\deviceID\
2. Right-click to UpdateParam.bat -> run as administrator, then your settings have been updated.
3. Restart you computer.

### Modify registry value using INF file ###

1. To enable the registry key, Please remove character ';' to uncomment the statement
2. Registry key is allocated at 3 position:
   - Parameters keys: [silabser.AddService.AddReg] directives
   - Software keys:   [silabser.AddReg] directives
   - Hardware keys:   [SiLabsDDInstallSection.HW.AddReg] directives

SUPPORT
-------
For technical support please visit the Silicon Labs support site:

https://www.silabs.com/support

******************************************************************************
    RELEASE NOTES FOR 11.3.0 (2023-05-26)

Changes for VCP Driver
==============================================================================
MCUSW-1386   | Fix bug in get Modem status stress test
MCUSW-1404   | Change the .inf file to enable the purge buffer command
MCUSW-1405   | Create the .bat and .reg files for the customer to easily update
             | registry parameters VCP driver
MCUSW-1395   | Microsoft Windows Certified ("WHQL Certified") for Windows 11
             | version 22H2, Windows 10 21h2 and Windows 10 RS5.

******************************************************************************
    RELEASE NOTES FOR 11.2.0 (2022-10-21)

Changes for VCP Driver
==============================================================================
MCUSW-415    | Remove code paths for XP vs not XP which is used for           
             | UsingWindows2000.                                              
MCUSW-416    | Improve debug statement readability by adding device specific  
             | information.                                                   
MCUSW-523    | add instruction how to setting up registry in .inf file.       
MCUSW-532    | Fix Automatic handshaking on RTS/CTS, and driver buffers       
             | overran at high baud rate.                                     
MCUSW-1285   | add DisableIoctlIOCTL_SERIAL_PURGE in .inf file to prevent data
             | lost in close.
******************************************************************************
    RELEASE NOTES FOR 11.1.0 (2022-03-21)

Changes for VCP Driver
==============================================================================
MCUSW-803    | CP210x device needs to send Xoff to the other side device 
             | (FTDI for example) when Windows goes to sleep
MCUSW-1038   | Fix DFx problem on Windows 11
MCUSW-1039   | Do HLK DFx testing for Windows VCP driver version 11.1.0
MCUSW-1045   | Update file version and driver version for Windows VCP 
             | driver version 11.1.0
MCUSW-1047   | Make the Windows VCP driver pass SDV
MCUSW-1048   | Microsoft Windows Certified ("WHQL Certified") for Windows 11
             | version 21H2
MCUSW-1049   | Using Dynamic api to make Windows VCP driver to be compatible
             | with different versions of Windows (Mininum required is Windows
             | 10 version 1803)
******************************************************************************
    RELEASE NOTES FOR 11.0.0 (2021-11-05)

Changes for VCP Driver
==============================================================================
MCUSW-176    | Add report SERIAL_ERROR_QUEUEOVERRUN when driver-side receive 
             | buffer is overrun
MCUSW-889    | Fixed HLK Test error: Static Tools Logo Test
MCUSW-749    | Fixed issue that RTS is not set to high when Windows goes to 
             | sleep to make sure incoming data to CP210x won't be lost when 
             | Windows is in sleeping state
MCUSW-841    | Removed installer to make a standalone driver package. Users
             | need to use INF file to install the driver instead
MCUSW-906    | Add Microsoft Windows Certified ("WHQL Certified") for Windows 11
             | version 21H2

******************************************************************************
    RELEASE NOTES FOR 10.1.10 (2021-01-13)

Changes for VCP Driver
==============================================================================
MCUSW-651    | Support baud rate up to 2187500 for CP2102, CP2104, CP2109
MCUSW-685    | Fixed the Blue Screen issue when running Windows Hardware Lab   
             | Kit for customized driver                                       
MCUSW-783    | Microsoft Windows Certified (aka "WHQL Certified") for Windows  
             | 10 version 20H2 (2020-10-20)                                    

******************************************************************************
    RELEASE NOTES FOR 10.1.9 (2020-07-30)

Changes for VCP Driver
==============================================================================
MCUSW-566    | Remove sanity/error checking on IOCTL_SERIAL_SET_BAUD_RATE for  
             | CP2103 devices.                                                 
MCUSW-596    | Microsoft Windows Certified (aka "WHQL Certified") for Windows  
             | 10 version 2004 (2020-05-27)                                    
MCUSW-619    | Support for Directed PoFx (DFx - Directed Power Management      
             | Framework).                                                     

******************************************************************************
    RELEASE NOTES FOR 10.1.8 (2019-06-24 (DriverVer = 06/20/2019,10.1.8.2466))

Changes for VCP Driver
==============================================================================
MCUSW-412    | Certified for Windows 10 RS6.                                   
MCUSW-484    | WDFVERIFY() added to the driver. Configurable via Registry.    
MCUSW-493    | Improved the tagging/tracking and parent-hierarchy of framework
             | objects and framework object reference counts. 
MCUSW-495    | Clear RTS on CloseHandle().                                     
MCUSW-508    | IOCTL_SERIAL_GET_COMMSTATUS refactored to reduce USB-bus        
             | bandwidth, while still offering timely reporting.               
MCUSW-518    | WDFVerifier parameter ForceLogsInMiniDump Registry parameter    
             | added for improved supportability.                              
MCUSW-519    | Resolve an SDV-identified issue: do not double-complete a       
             | Request on error paths.                                         
MCUSW-526    | Creates the framework USB device object with client contract    
             | version USBD_CLIENT_CONTRACT_VERSION_602/0x602 (I.e. Register   
             | with "new" (to Windows 8) Windows USB driver stack).            

******************************************************************************
    RELEASE NOTES FOR 10.1.7 (2019-03-26 (DriverVer = 03/26/2019,10.1.7.2399))

Changes for VCP Driver
==============================================================================
MCUSW-473    | Fix length of nul-terminated legacy Dos Name string written to  
             | HARDWARE\DEVICEMAP\SERIALCOMM Registry key.                     
MCUSW-483    | Fixed bug for Max Baud rate for CP2101, CP2104, CP2105 and
             | CP2108 devices.                                                        

******************************************************************************
    RELEASE NOTES FOR 10.1.6 (2019-03-19 (DriverVer = 03/15/2019,10.1.6.2388))

Changes for VCP Driver
==============================================================================
MCUSW-445    | Fix a blue-screen system crash bug with handling of ioctl       
             | IOCTL_SERIAL_WAIT_ON_MASK during power state changes.           

******************************************************************************
    RELEASE NOTES FOR 10.1.5 (2019-02-19 (DriverVer = 02/19/2019,10.1.5.2368))

Changes for VCP Driver
==============================================================================
MCUSW-414    | Implement an undocumented Registry-configured feature to ignore 
             | IOCTL_SERIAL_PURGE.                                             
MCUSW-417    | Read many of the Registry "parameter"-type settings first from  
             | the "parameters key" and then from the "hardware key", with the 
             | "hardware key" taking precedence (allows "driver wide, all      
             | devices" setting, but provides the capability to specify per-   
             | device settings (before we only supported per-device            
             | settings)).                                                     
             |                                                                 
MCUSW-439    | Fixed a bug whereby Close()-Open() on a CP2102N could get USB   
             | data toggle confused (I.e. issue USB CLEAR_FEATURE(HALT) to     
             | bulk endpoints to reset data toggle back to DATA0).             
MCUSW-449    | Fix a Max Baud Rate bug (use device-specific MaxBauds (from the 
             | data-sheets): 3 Mbaud for CP2102N, 1 Mbaud for all other CP210x 
             | devices.).                                                      
MCUSW-450    | Fix Verification BSOD (race condition in the VCP device driver  
             | that can cause double completions): Only call                   
             | DetachForCompletionUNcancelable on success of UNmark as         
             | cancelable in handling of IOCTL_SERIAL_WAIT_ON_MASK-related     
             | requests.                                                       

******************************************************************************
    RELEASE NOTES FOR 10.1.4 (2018-12-07 (DriverVer = 11/26/2018,10.1.4.2290))

Changes for VCP Driver
==============================================================================
MCUSW-134    | Fixed an issue with handling of IOCTL_SERIAL_SET_WAIT_MASK,     
             | IOCTL_SERIAL_WAIT_ON_MASK, with the SERIAL_EV_RXCHAR event and  
             | data arriving from the device into the driver. Previously, an   
             | indication of arriving data was made before making the data     
             | available, causing, in some conditions, subsequent requests for 
             | data after notification of data available to not deliver any    
             | data.                                                           
MCUSW-144    | Onecore-based editions of Windows 10 (I.e. Windows 10 IoT Core) 
             | do not, by design, create PortName entries in the Registry to   
             | specify the device's legacy DOS name (I.e. COM<n).              
             | Consequently, VCP enhanced to not treat this as a failing       
             | condition and to continue without creating legacy COM<n> DOS    
             | devices.                                                        
MCUSW-148    | Rearchitected into two VCP driver packages:                     
             |  1) Windows 7 and later Desktop Editions x86 and x64 driver     
             | package, and                                                    
             |  2) Windows Universal (10 and later; Desktop, tablet, mobile,   
             | embedded) x86, x64, ARM, ARM64 driver package.                  
MCUSW-214    | Windows 10 Universal driver release (I.e. no Windows 7, 8 or    
             | 8.1 support)                                                    
MCUSW-352    | Workaround to issue where close during receipt of serial data   
             | caused CP2102N to hang.                                         
MCUSW-369    | Certified for Windows 10 RS5.                                   
MCUSW-393    | Fix bug due to some BaudRate-related math causing a divide-by-  
             | zero.                                                           
MCUSW-396    | Be defensive against the impossible case of getting a NULL      
             | object in the object completion routine.                        

******************************************************************************
    RELEASE NOTES FOR 10.1.3 (2018-05-29)

Changes for VCP Driver
==============================================================================
MCUSW-326    | Clear DTR on CloseHandle().                                     

******************************************************************************
    RELEASE NOTES FOR 10.1.2 (2018-05-14)

Changes for VCP Driver
==============================================================================
MCUSW-134    | Fixed an issue with handling of IOCTL_SERIAL_SET_WAIT_MASK,     
             | IOCTL_SERIAL_WAIT_ON_MASK, with the SERIAL_EV_RXCHAR event and  
             | data arriving from the device into the driver. Previously, an   
             | indication of arriving data was made before making the data     
             | available, causing, in some conditions, subsequent requests for 
             | data after notification of data available to not deliver any    
             | data.                                                           
MCUSW-211    | Windows 10 Universal driver release (I.e. no Windows 7, 8 or    
             | 8.1 support)                                                    
MCUSW-288    | Fix IOCTL_SERIAL_GET_PROPERTIES.                                
MCUSW-291    | Fix IOCTL_SERIAL_GET_PROPERTIES/SERIAL_COMMPROP for CP210x-like 
             | "Voice MB v2.0" device.                                         
MCUSW-315    | Certified for RS4/1803.                                         

******************************************************************************
    RELEASE NOTES FOR 10.1.1 (DriverVer=11/15/2017,10.1.1.1951)

Changes for VCP Driver
==============================================================================
MCUSW-134    | Fixed an issue with handling of IOCTL_SERIAL_SET_WAIT_MASK,
             | IOCTL_SERIAL_WAIT_ON_MASK, with the SERIAL_EV_RXCHAR event
             | and data arriving from the device into the driver. Previously,
             | an indication of arriving data was made before making the data
             | available, causing, in some conditions, subsequent requests
             | for data after notification of data available to not deliver
             | any data. 

******************************************************************************
LEGACY HISTORY
--------------
Everything below is the shared development history before creation of the
Windows 10 Universal driver.  Everything above is development history of
the Universal driver.

******************************************************************************
    RELEASE NOTES FOR 6.7.5 (2017-10-13)

Changes for VCP Driver
==============================================================================
MCUSW-17     | IOCTL_SERIAL_GET_STATUS TransmittedCount fixed.                 
MCUSW-19     | CP210x_GET_CONFIG_DESCRIPTOR_IOCTL returned byte count fixed.   
MCUSW-21     | Revert IOCTL_SERIAL_GET_COMMSTATUS behaviour to return cached   
             | information (reverse slowdown reported with v6.7.4 in some      
             | applications)                                                   
             |                                                                 
             | Improve windbg logging, w.r.t. doing less when logging is not   
             | enabled (say, Release builds), or when particular subsystem is  
             | not enabled for logging.                                        
             |                                                                 
MCUSW-110    | Windows 10 certified against RS2 (Creators Update).             
MCUSW-207    | In a failed initialization, discard a reference to dynamically  
             | allocated memory once memory has been freed.                    
MCUSW-234    | timestamp SHA2 Signatures with SHA2 timestamps                  

******************************************************************************
    RELEASE NOTES FOR 6.7.4.261 (2017/01/30)

- Device Guard compliant
- CP210XFW-747: Add 3 new parallel PIDs one each for the single-, dual- &
  quad-port CP210x devices (to be distributed via Windows Update)
- CP210XFW-741: Fix driver to use correct interface string index for the
  multi-interface CP210x devices (CP2105 & CP2108). Return iProduct string
  for other CP210x devices.
- CP210XFW-713: Add protection against IRP_MJ_CLOSE coming before
  IRP_MJ_CLEANUP. In such case EvtFileCleanup callback was called with 0
  FileObject, causeing a crash. Serenum is suspected of causing this, even
  though there is no proof except that it's present, was introduced recently
  and this crash was never registered before.
- CP210XFW-691: Fixed race between timer activation and request cancelation
  during processing of read rwquests.
- Changed raw WDF read request timer to our wrapper.
- CP210XFW-693: bugfix: WMI command "wmic path Win32_SerialPort get
  Availability^, DeviceID^, Name" is unable to enumerate the port.
- CP210XFW-686: EvtRequestCancel for wait mask IRP crashed because the
  request was already completed. It didn't serialize well with other places
  that can complete it. It looked like XOff IRP may have the same proble. This
  patch is adding an extra check into *all* other EvtRequestCancel functions
  to make sure this doesn't happen again.
- Changed IOCTLs returning polled-cached MDMSTS to explicitly read the
  status. Use reg value DisableHwAccessInModemStatusIoctls to revert this
  new functionality to old behavior.
- Improved debug prints.
- SerialDbgPrintEx used 1K of stack for the string, reduced to 256.
- Resolved many static Code Analysis warnings
- Added accounting for data in chip's TX queue. Added translation of
  COMM_STATUS::ulErrors into SERIAL_EV_BREAK and SERIAL_EV_ERR.
- CP210XFW-549, CP210XFW-536, CP210XFW-546: Generate events for
  IOCTL_SERIAL_SET_WAIT_MASK from COMM_STATUS::ulErrors. Can be disabled by
  DisableCommStatusPolling reg value.
- Added spinlock around ModemStatus change detection. Refactored modem
  status event signalling to use common function.
- Move passive level functions into the paged section.
- MCUFW-740: Made device close operation wait for chip's Tx queue to empty.
  Added registry settings DisableTxEmptyCheckInClose and
  TxEmptyTimeoutOnCloseInMs.
- Improve control transfer debug prints and clean up code, otherwise no
  functional changes.
- MCUFW-740: Fixed EV_TXEMPTY to account for bytes in chip's Tx queue.
- MCUFW-740: New functions to sync access to comm error storage from
  multiple threads.
- Added DisableTxEmptyCheckInGetCommStatusIoctl reg value.
- Refactor control request I/O. MCUFW-740: Fixed
  IOCTL_SERIAL_GET_COMMSTATUS.
- MCUFW-740: Made device close operation wait for chip's Tx queue to empty.
  Added registry settings DisableTxEmptyCheckInClose and
  TxEmptyTimeoutOnCloseInMs.
- CP210XFW-648: Set a three second timeout on
  WdfUsbTargetDeviceSendControlTransferSynchronously().

******************************************************************************
    RELEASE NOTES FOR 6.7.3 (2016/03/03)

- Down-rev the verison of KMDF the driver uses (CP210XFW-591. Use version of
  KMDF natively included on Windows release)
- Bug fix of blue-screen system crash (CP210XFW-575. driver tries to clear a
  Cancel Routine in a Request that doesn't have it.)

******************************************************************************
    RELEASE NOTES FOR 6.7.2 (2015/11/23)

- Unified Windows 7, 8, 8.1 & 10 support (XP, Vista and Server 2003
  available in version 6.7).
- ARM support added for Windows 10 and Windows 10 IoT Core.
- Silicon Labs-specific Serial Enumeration driver silabenm removed in favor
  of the Windows "in-box" serenm.
- UpperFilter Serial Enumeration driver not enabled by default
- Updated to latest Microsoft build tools
- Resolved /W4 compilation warnings
- Resolved code analysis warnings
- Added a registry value ControlHandShakeForcedSetBits that can force
  certain bits in the ControlHandShake variable to always be set.
- Add SAL-annotations to API header files.
- Bugfix an invalid memory access on device stop.
- Standardize branding Properties resources across all deliverables.
- Digitally sign all signable deliverables.
- Rewrote driver synchronization for data transmission paths.
- Resolve bugs arising from extended stress test.
- Added diagnostic variables to device extension.
- Bugfix a Write IRP stuck forever cauding bugcheck 9f-4 if call to USB
  returns with error.
- Bugfix "packetized write" timeout may fail to act. And improved debug
  prints.
- New reg value DisableS0Idle (default: 0) to replace EnablePowerManagewment
  (default: 0 which actually ment "enable"). Also, DisableS0Idle=1 now
  forces AllowIdleWhileOpen to 0.
- Driver ignores BreakOnEntry, DebugLevel and DebugFlag in registry.
- New CP2108 bug workarounds - GET_LINE_CTL byte swap and tx_empty().
- Fixed crash in read path.
- Simplified, commented and synchronized with NEWSTUFF EvtIoStop and
  EvtIoResume.
- Fixed memory leak on device removal when multiple devices are present.
- Bugfix Read IRP may never complete if other read IRPs are already waiting
  when it arrives.
- Add CP2102N part numbers. Hnadle new part numbers in
  WriteLatch()/ReadLatch().
- Resolve HCK INF warnings that became errors on HLK.
- Bugfix: Potential invalid memory access on device stop.
- Fixed possible memory overrun when writing CP2108 latch.
- Cumulative collection of improvements (due to code analysis, application
  of latest toolset, etc.) and bug fixes.

******************************************************************************
    RELEASE NOTES FOR 6.7.1 (2015/06/29)

- Added certification for Windows 10 Preview (Note: Windows 10 only;
  use v6.7 for Windows prior to Windows 10)

******************************************************************************
    RELEASE NOTES FOR 6.7 (2014/04/11)

- Added vendor-specific commands to the driver that do not affect normal
  operation with standard CP210x devices.
- Modified write behavior to packetize data as a work around for a rare
  USB 2.0 hub behavior seen only in Windows XP (x86).

******************************************************************************
    RELEASE NOTES FOR 6.6.1 (2013/10/24)

- Added certification for Windows 8.1
- Added support for CP2108 devices
- Corrected bug where OS would hang on repetition of many rapid open/closes on
  certain systems.

******************************************************************************
    RELEASE NOTES FOR 6.6

- Moving installer format to DPInst
- Supported under Windows 8
- Corrected bug in total write timeout calculation
- Corrected bug where EV_BREAK event could be misreported based on incoming
  data
- Corrected another BSOD corner case regarding write cancellation

******************************************************************************
    RELEASE NOTES FOR 6.5.3

- Corrected BSOD corner case for a write cancellation
- Corrected memory leak that occurs when a device is plugged/unplugged
  rapidly enough to allow driver startup function to fail

******************************************************************************
    RELEASE NOTES FOR 6.5

- Corrected BSOD corner case issue for handling control requests
- Corrected issue where USB 3.0 hubs would deliver data to the driver out
  of order

******************************************************************************
    RELEASE NOTES FOR 6.4

- Corrected multiple BSOD issues by updating request handling for control
  requests to the USB device, and the write completion method
- Corrected device removal routine to also undo the COM port naming in the
  registry at removal time instead of when the device is closed after the
  removal.

******************************************************************************
    RELEASE NOTES FOR 6.3a

- Updated to 3.2 DriverInstaller to correct a bug seen when updating from an
  old driver installer version	

******************************************************************************
    RELEASE NOTES FOR 6.3

- Corrected a bug introduced in 6.2 which caused BSOD during surprise removal.
- Corrected a bug found in I/O cancellation corner case

******************************************************************************
    RELEASE NOTES FOR 6.2

- Corrected return value for DeviceIoControl() and other COM API functions
  once the device is removed to properly show ERROR_ACCESS_DENIED (0x05)
  instead of ERROR_BAD_COMMAND in GetLastError()
- Corrected bug in DTR/RTS reporting latency seen if you set DTR/RTS and ask
  for it before the device has reported it to the host - now when it is
  written it reads back immediately
- Corrected several USB requests that were improperly defined as device
  requests when they are actually interface requests - this doesn't exhibit
  and bugs in current single interface devices but was changed to be complete
  and correct
- Added support for CP2104 and CP2105 devices	

******************************************************************************
    RELEASE NOTES FOR 6.1

- Corrected a memory leak which could bog the system down after extended use
  of a contiuously opened COM port, and conditionally yield bluescreens on
  certain systems
- Corrected a problem where an IO reqest would sometimes return a busy
  status to user mode, instead the queue is restarted if necessary before
  adding an IO request to the queue
- Corrected a condition which would blue screen on cancelling write request
  that hasn't been fully sent out USB
- Corrected the Capabilites return value, which incorrectly reported that
  timeouts are not supported
- Corrected several Queue size return values, which affected behavior in the
  MSCOMM control
- Corrected DTR/RTS value on device insertion, visible when Serial
  Enumeration is disabled
- Corrected the ability to override Baud Rate and Line Control from the INF
  file

******************************************************************************
    RELEASE NOTES FOR 6.0

- Corrected multiple blue screens and driver hangs related to race
  conditions in the driver
- Corrected problem where driver hangs when 4 or more devices are connected
  to a single transaction translator hub
- Corrected bugs that prohibited serial enumeration
- Corrected problem where IO requests were not completed/cancelled on a
  close
- Corrected problem with dialing out or PPP connections
- Created IO queueing mechanism so that multiple reads, writes, etc. can be
  queued and waited on

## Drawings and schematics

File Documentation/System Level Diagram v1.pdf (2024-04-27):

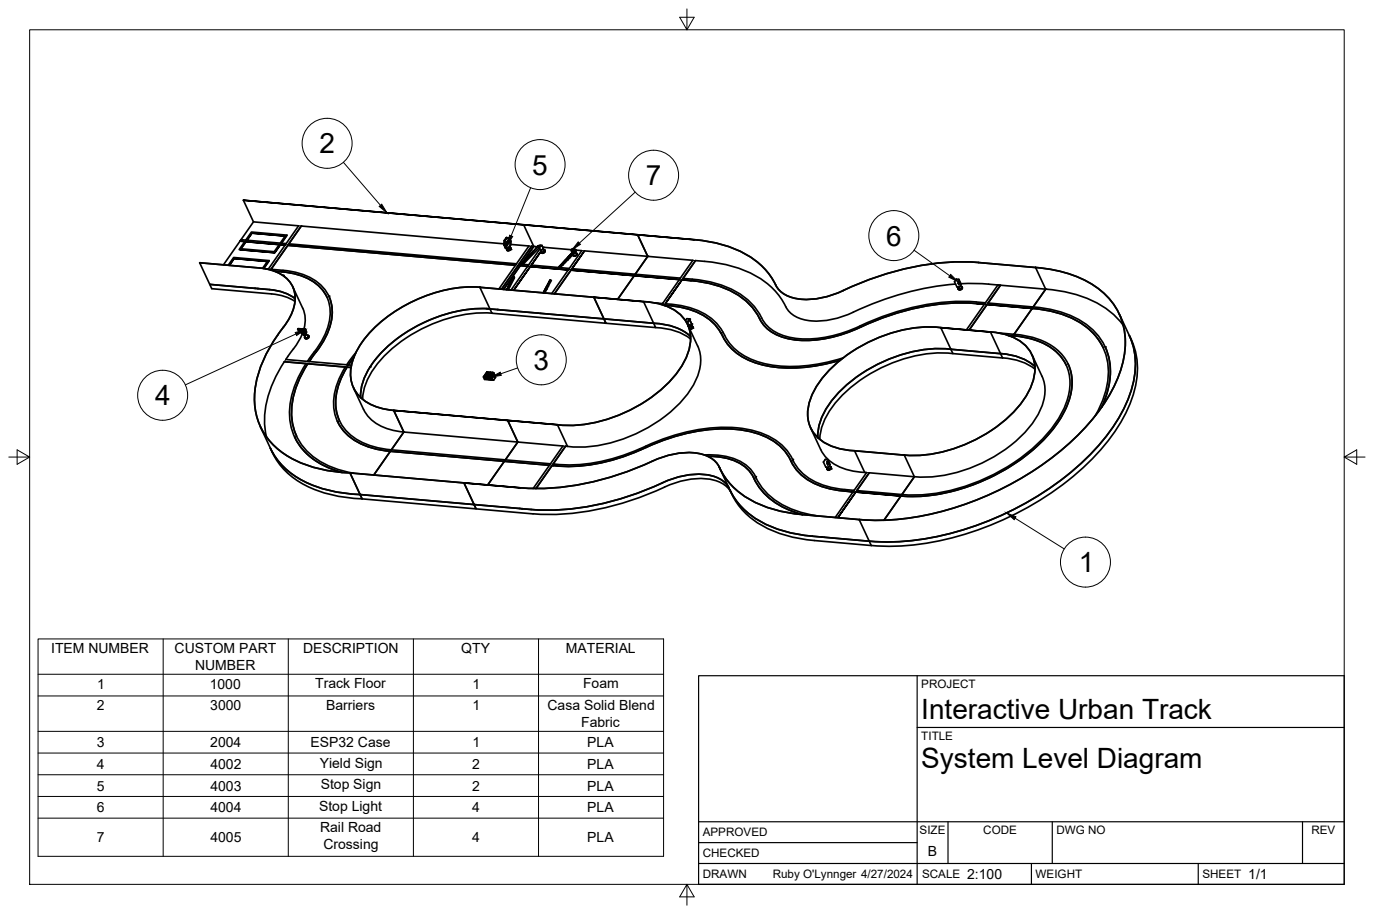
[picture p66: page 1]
Ruby O'Lynnger 4/27/2024; Track Floor; Foam; ITEM NUMBER; CUSTOM PART

PROJECT
Interactive Urban Track
System Level Diagram

2 | 3000 | Barriers | 1 | Casa Solid Blend Fabric

3 | 2004 | ESP32 Case | 1 | PLA
4 | 4002 | Yield Sign | 2 | PLA
5 | 4003 | Stop Sign | 2 | PLA
6 | 4004 | Stop Light | 4 | PLA
7 | 4005 | Rail Road Crossing | 4 | PLA

APPROVED | SIZE B | CODE | DWG NO | REV

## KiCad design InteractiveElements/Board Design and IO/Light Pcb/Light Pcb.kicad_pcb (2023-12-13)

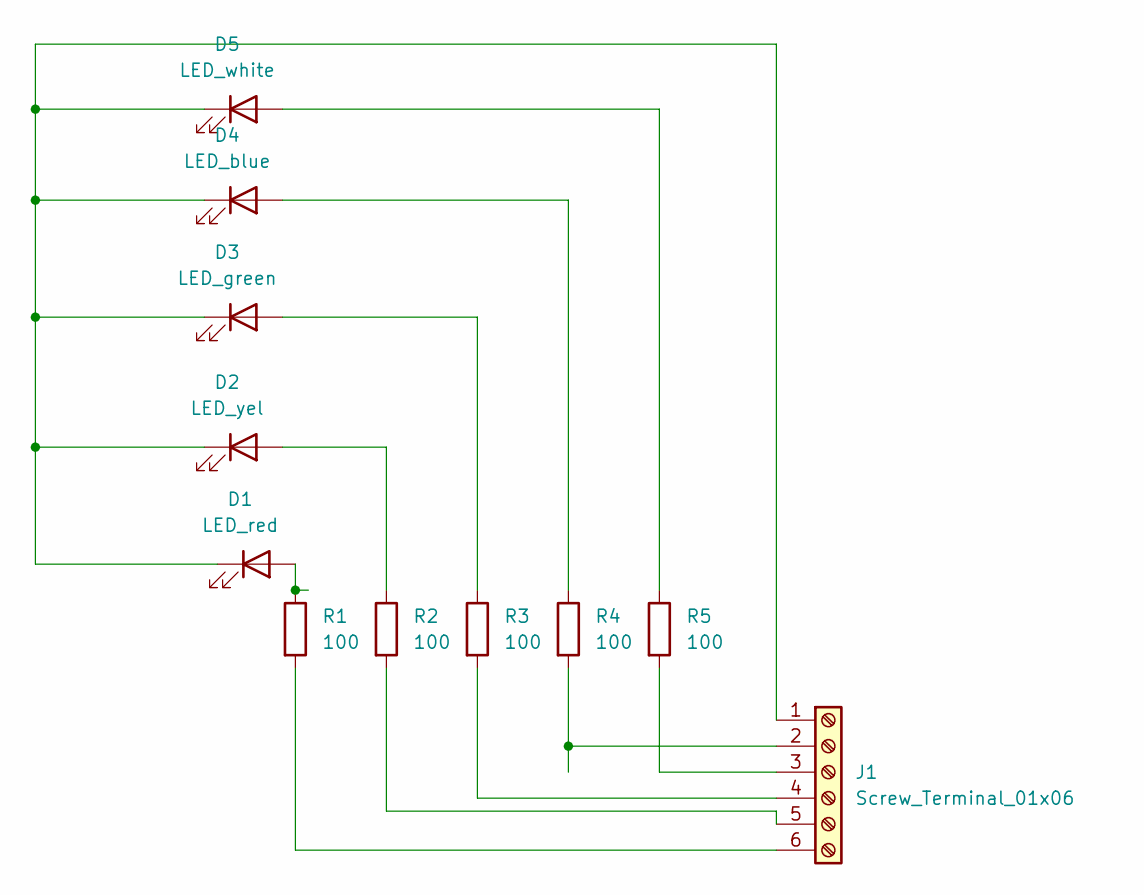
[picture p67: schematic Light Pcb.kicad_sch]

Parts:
D1: LED_red; LED_D5.0mm_Clear
D2: LED_yel; LED_D5.0mm_Clear
D3: LED_green; LED_D5.0mm_Clear
D4: LED_blue; LED_D5.0mm_Clear
D5: LED_white; LED_D5.0mm_Clear
J1: Screw_Terminal_01x06; PinHeader_1x06_P2.54mm_Vertical
R1, R2, R3, R4, R5: 100; R_Axial_DIN0204_L3.6mm_D1.6mm_P5.08mm_Horizontal

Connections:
unnamed: D1.2 (A), R1.1
unnamed: D1.1 (K), D2.1 (K), D3.1 (K), D4.1 (K), D5.1 (K), J1.1
unnamed: D2.2 (A), R2.1
unnamed: D3.2 (A), R3.1
unnamed: D4.2 (A), R4.1
unnamed: D5.2 (A), R5.1
unnamed: J1.2, R4.2
unnamed: J1.3, R5.2
unnamed: J1.4, R3.2
unnamed: J1.5, R2.2
unnamed: J1.6, R1.2

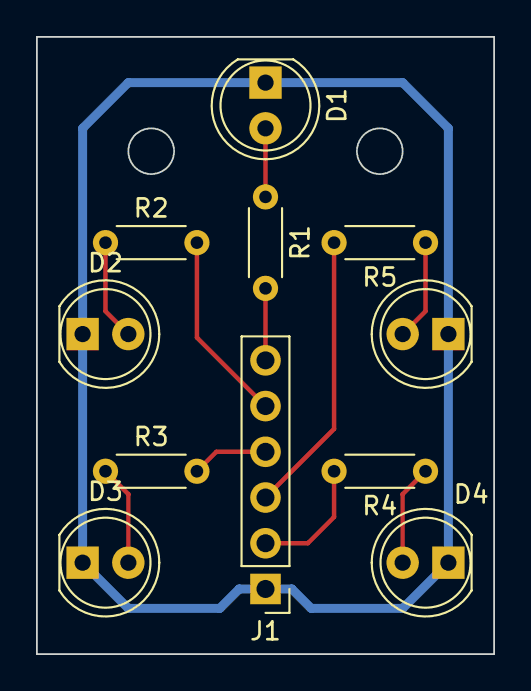
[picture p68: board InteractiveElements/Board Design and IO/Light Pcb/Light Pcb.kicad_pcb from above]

Board: 2 copper layers, 25.4 x 34.3 mm, 11 parts (0 on the bottom side), 11 nets.

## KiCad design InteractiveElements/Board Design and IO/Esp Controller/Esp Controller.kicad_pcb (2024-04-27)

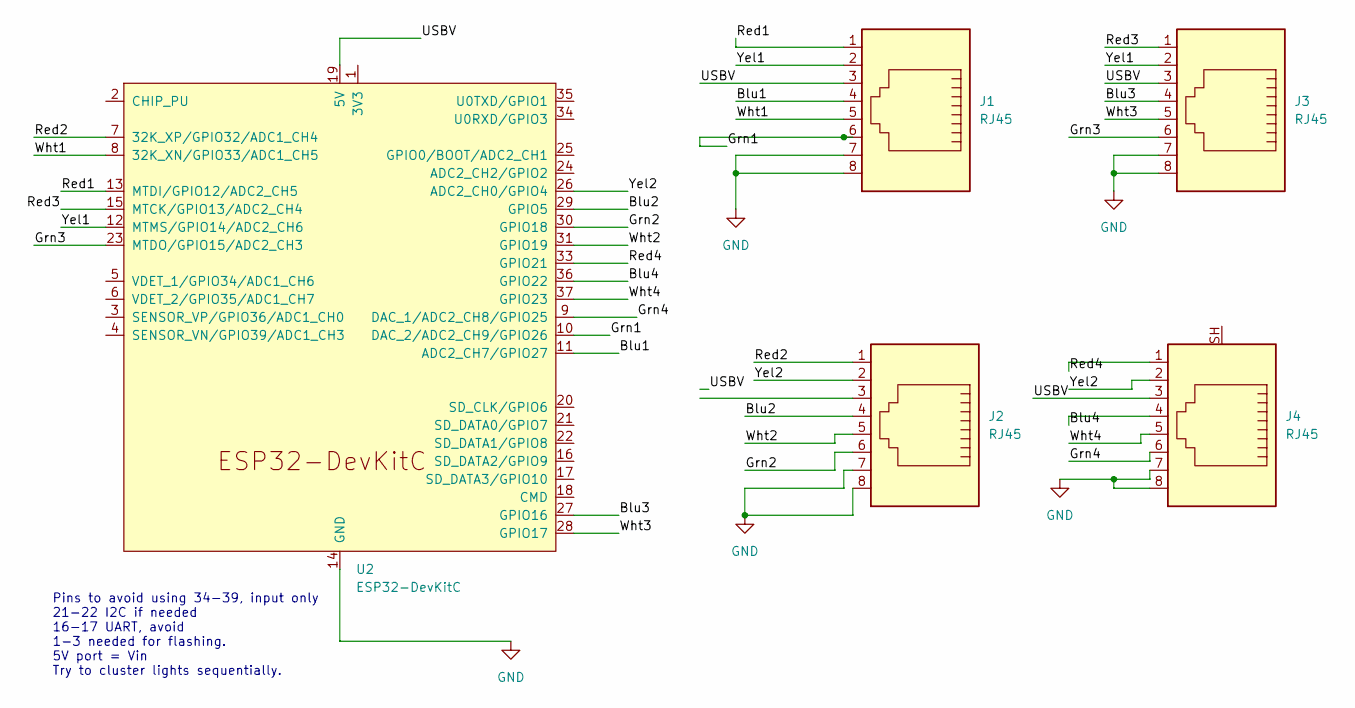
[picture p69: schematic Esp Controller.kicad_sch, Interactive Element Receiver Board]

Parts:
J1, J2, J3, J4: RJ45; RJ45_Amphenol_54602-x08_Horizontal
U2: ESP32-DevKitC

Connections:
/Blu1: J1.4, U2.11 (ADC2_CH7/GPIO27)
/Blu2: J2.4, U2.29 (GPIO5)
/Blu3: J3.4, U2.27 (GPIO16)
/Blu4: J4.4, U2.36 (GPIO22)
/Grn1: J1.6, U2.10 (DAC_2/ADC2_CH9/GPIO26)
/Grn2: J2.6, U2.30 (GPIO18)
/Grn3: J3.6, U2.23 (MTDO/GPIO15/ADC2_CH3)
/Grn4: J4.6, U2.9 (DAC_1/ADC2_CH8/GPIO25)
/Red1: J1.1, U2.13 (MTDI/GPIO12/ADC2_CH5)
/Red2: J2.1, U2.7 (32K_XP/GPIO32/ADC1_CH4)
/Red3: J3.1, U2.15 (MTCK/GPIO13/ADC2_CH4)
/Red4: J4.1, U2.33 (GPIO21)
/USBV: J1.3, J2.3, J3.3, J4.3, U2.19 (5V)
/Wht1: J1.5, U2.8 (32K_XN/GPIO33/ADC1_CH5)
/Wht2: J2.5, U2.31 (GPIO19)
/Wht3: J3.5, U2.28 (GPIO17)
/Wht4: J4.5, U2.37 (GPIO23)
/Yel1: J1.2, J3.2, U2.12 (MTMS/GPIO14/ADC2_CH6)
/Yel2: J2.2, J4.2, U2.26 (ADC2_CH0/GPIO4)
GND: J1.7, J1.8, J2.7, J2.8, J3.7, J3.8, J4.7, J4.8, U2.14 (GND), U2.32 (GND), U2.38 (GND)

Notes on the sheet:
Pins to avoid using 34-39, input only 21-22 I2C if needed 16-17 UART, avoid 1-3 needed for flashing. 5V port = Vin Try to cluster lights sequentially.

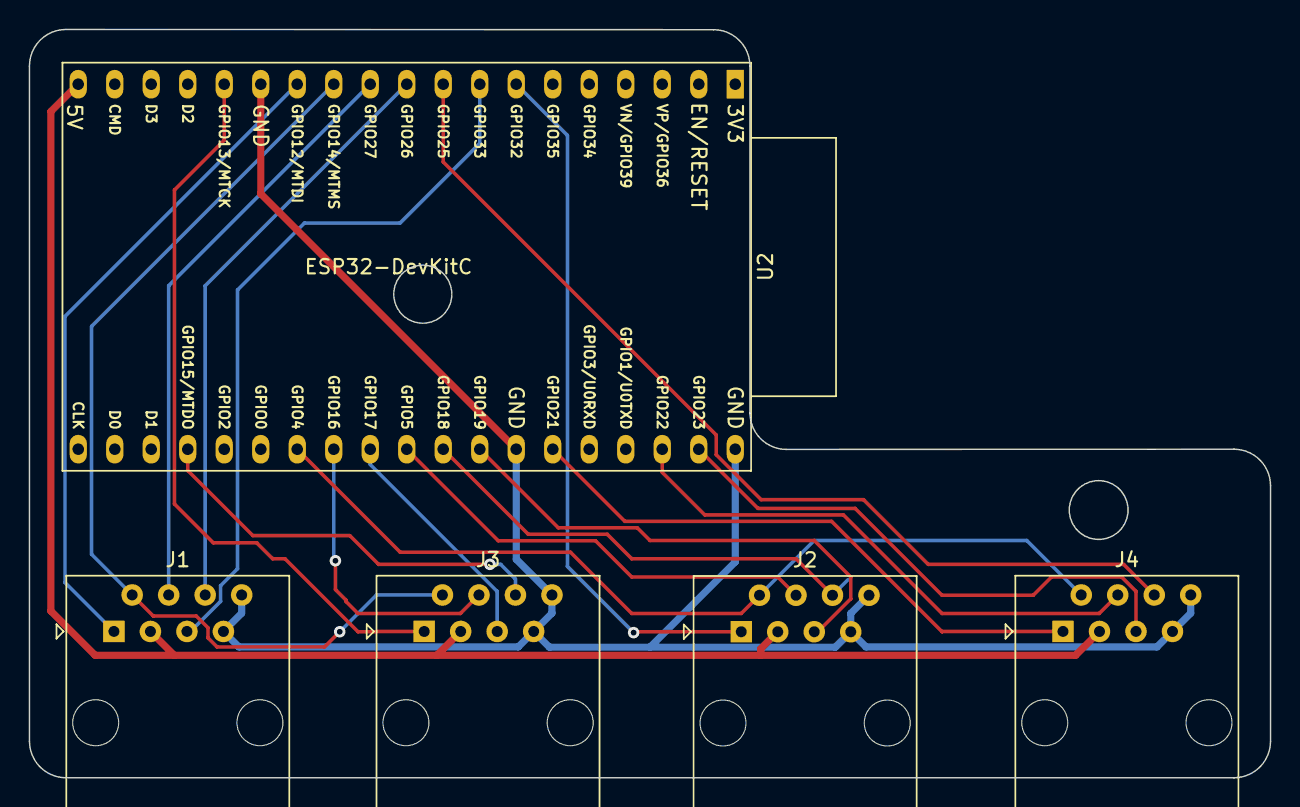
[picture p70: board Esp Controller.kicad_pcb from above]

Board: 2 copper layers, 86.4 x 52.1 mm, 5 parts (0 on the bottom side), 20 nets.

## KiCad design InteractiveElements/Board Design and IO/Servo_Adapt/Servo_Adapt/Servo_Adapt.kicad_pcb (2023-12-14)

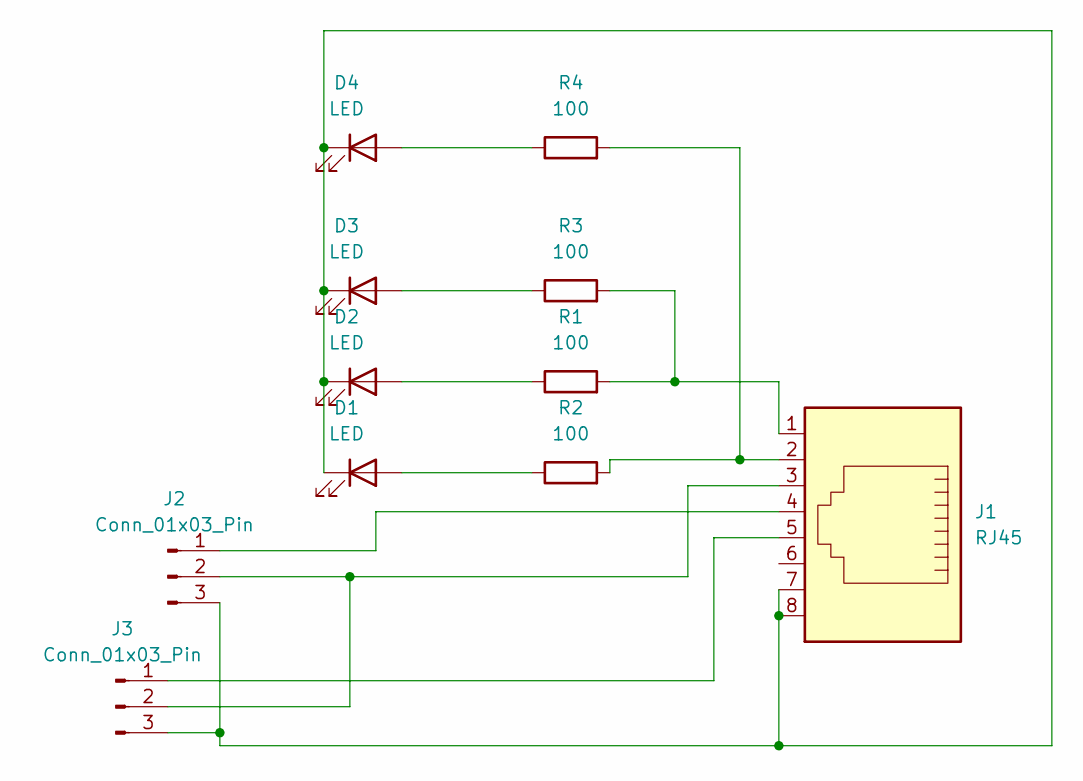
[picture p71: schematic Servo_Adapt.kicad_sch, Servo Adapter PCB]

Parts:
D1, D2, D3, D4: LED; LED_D5.0mm
J1: RJ45; RJ45_Amphenol_54602-x08_Horizontal
J2, J3: Conn_01x03_Pin; PinHeader_1x03_P2.54mm_Vertical
R1, R2, R3, R4: 100; R_Axial_DIN0207_L6.3mm_D2.5mm_P10.16mm_Horizontal

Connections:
unnamed: D1.2 (A), R2.1
unnamed: D1.1 (K), D2.1 (K), D3.1 (K), D4.1 (K), J1.7, J1.8, J2.3, J3.3
unnamed: D2.2 (A), R1.1
unnamed: D3.2 (A), R3.1
unnamed: D4.2 (A), R4.1
unnamed: J1.1, R1.2, R3.2
unnamed: J1.2, R2.2, R4.2
unnamed: J1.4, J2.1
unnamed: J1.3, J2.2, J3.2
unnamed: J1.5, J3.1

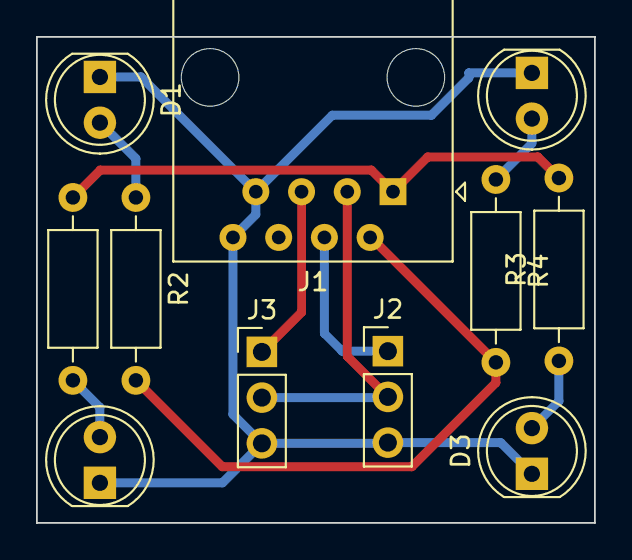
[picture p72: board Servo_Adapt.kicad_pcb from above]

Board: 2 copper layers, 31.0 x 27.0 mm, 11 parts (0 on the bottom side), 10 nets.

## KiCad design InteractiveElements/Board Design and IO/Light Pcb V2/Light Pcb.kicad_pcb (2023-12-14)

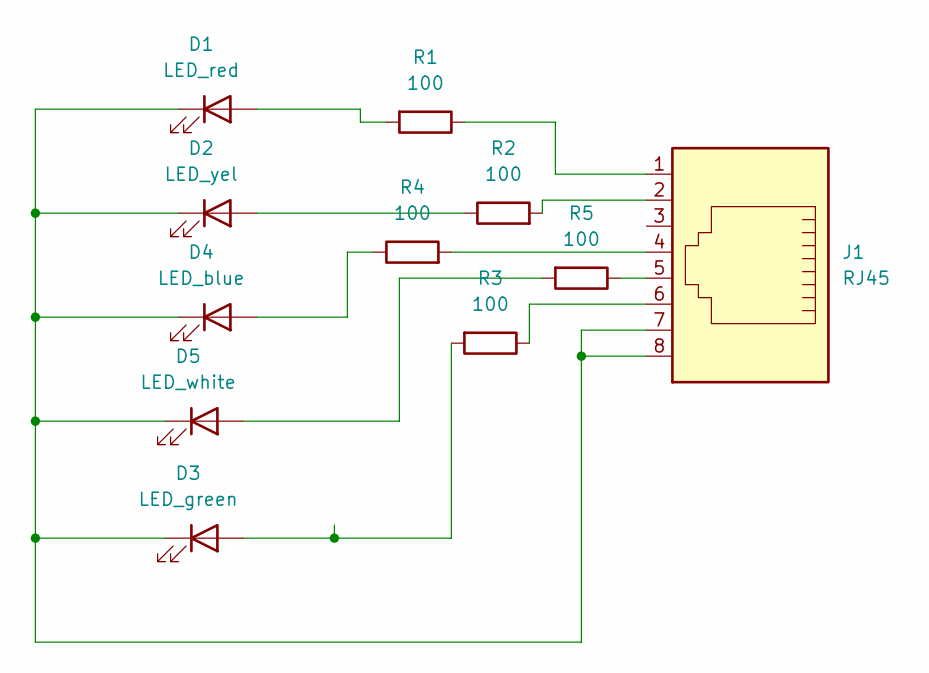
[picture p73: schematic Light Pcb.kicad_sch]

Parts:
D1: LED_red; LED_D5.0mm_Clear
D2: LED_yel; LED_D5.0mm_Clear
D3: LED_green; LED_D5.0mm_Clear
D4: LED_blue; LED_D5.0mm_Clear
D5: LED_white; LED_D5.0mm_Clear
J1: RJ45; RJ45_Amphenol_54602-x08_Horizontal
R1, R2, R3, R4, R5: 100; R_Axial_DIN0207_L6.3mm_D2.5mm_P7.62mm_Horizontal

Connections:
unnamed: D1.2 (A), R1.2
unnamed: D1.1 (K), D2.1 (K), D3.1 (K), D4.1 (K), D5.1 (K), J1.7, J1.8
unnamed: D2.2 (A), R2.1
unnamed: D3.2 (A), R3.2
unnamed: D4.2 (A), R4.1
unnamed: D5.2 (A), R5.2
unnamed: J1.1, R1.1
unnamed: J1.2, R2.2
unnamed: J1.4, R4.2
unnamed: J1.5, R5.1
unnamed: J1.6, R3.1

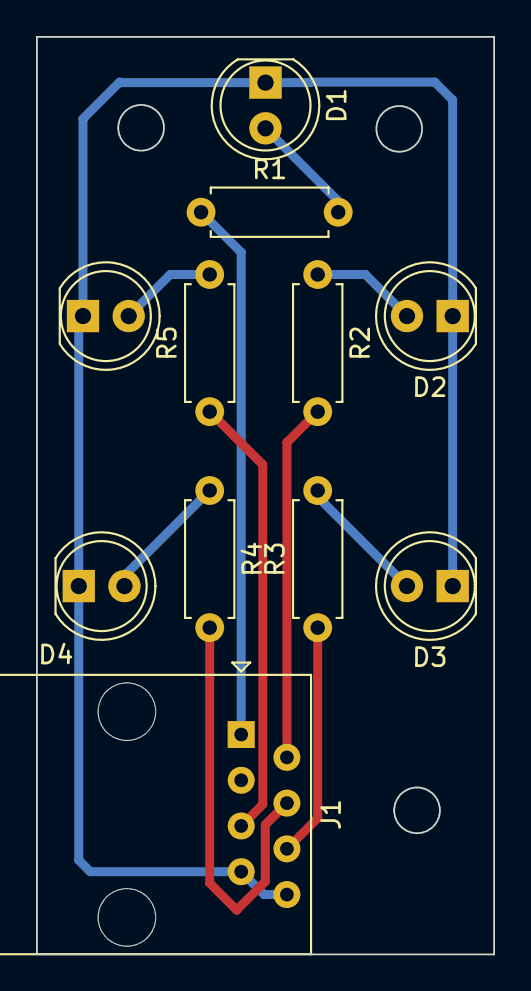
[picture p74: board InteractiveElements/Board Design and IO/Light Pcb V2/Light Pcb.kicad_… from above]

Board: 2 copper layers, 25.4 x 51.0 mm, 11 parts (0 on the bottom side), 11 nets.

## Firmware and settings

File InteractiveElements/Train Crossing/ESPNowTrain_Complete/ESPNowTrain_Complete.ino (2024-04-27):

#include <ESP32Servo.h>
#include <esp_now.h>
#include <WiFi.h>



typedef struct DataStruct {
  int Pair1;
  int Pair2;
  int Pair3;
  int Pair4;
  int Pair5;
  int Pair6;
  int Pair7;
  int Pair8;
  int Pair9;
  int Pair10;
  int Pair11;
  int Pair12;
  int Pair13;
  int Pair14;
  int Pair15;
  int Pair16;
}DataStruct;
DataStruct Data;

/* PCB Connections for Servo Adapter
Connector 1      Connector 2     Connector 3      Connector 4
LED side1 12              15              6                21 
Led Side2 14              4            Linked 1           Linked 2

Servo 1  25              19              8                23
Servo 2 27                5              7                22
*/
/* PCB Connections/ V2
Connector 1      Connector 2     Connector 3      Connector 4
Led Side 1 12         32              16                21 
Led Side 2 14         4            Linked 1           Linked 2

Servo 1 33            19              17                23
Servo 2 27            5              16                22
*/

/* Servo Pinouts per connector.
        J1    J2   LED1    LED2
Conn1   33    27   
Conn2   19    5
Conn3   17    16
Conn4   23    22
*/
Servo servo1, servo2, servo3, servo4;
#define CHANNEL 1
#define led1 12
#define led2 14
#define led3 32
#define led4 4
#define servopin1 33
#define servopin2 19
#define servopin3 17
#define servopin4 23
#define maxangle 150
#define minangle 0
#define timestep 40
#define swapspeed 6

int angle1 = 0;
int angle2 = 0;
int angle3 = 0;
int angle4 = 0;


void setup() {
  Serial.begin(9600);
  servo1.attach(servopin1);
  servo2.attach(servopin2);
  servo3.attach(servopin3);
  servo4.attach(servopin4);
  
  delay(100);
  servo1.write(angle1);
  servo2.write(180-angle2);
  servo3.write(angle3);
  servo4.write(180-angle4);
  WiFi.mode(WIFI_STA);

  //Init ESP-NOW
  if (esp_now_init() != ESP_OK) {
    Serial.println("Error initializing ESP-NOW");
    return;}
  esp_now_register_recv_cb(OnDataRecv);
 
}



void loop() {
  angle1 = servoangle(Data.Pair9,servo1,servo2,angle1,led1,led2);
  angle2 = servoangle(Data.Pair11,servo3,servo4,angle2,led3,led4);
  //#angle3 = servoangle(Data.Pair11,servo3,servo4,angle3,led3,led4);
  //angle4 = servoangle(Data.Pair12,servo3,servo4,angle4,led3,led4);
  delay(100);
  analogWrite(led1, 0);
  analogWrite(led2, 0);
  analogWrite(led3, 0);
  analogWrite(led4, 0);
}


int servoangle(int dest, Servo &obj, Servo &obj2, int angle, int l1, int l2) {
  if (dest >= maxangle) {
    dest = maxangle;
  }
  if (dest <= minangle) {
    dest = minangle;
  }
  if (angle < dest) {

    for (int i = angle; i <= dest; i++) {
      angle = i;
      obj.write(angle);
      obj2.write(180-angle);
      delay(timestep);
      trainled(i, l1, l2);
    }
  }

  if (angle > dest) {

    for (int i = angle; i >= dest; i--) {
      angle = i;
      obj.write(angle);
      obj2.write(180-angle);
      delay(timestep);
      trainled(i, l1, l2);
    }
  }

  return angle;
}

void trainled(int in, int l1, int l2) {
  if (in / 6 % 2 == 0) {
    analogWrite(l1, 255);
    analogWrite(l2, 0);
  } else {
    analogWrite(l1, 0);
    analogWrite(l2, 255);
  }
}

void OnDataRecv(const uint8_t * mac, const uint8_t *incomingData, int len) {
  memcpy(&Data, incomingData, sizeof(Data));
  Serial.print("Bytes received: ");
  Serial.println(len);
  Serial.print("Relevant Data: ");
  Serial.print(Data.Pair9);
  Serial.print(", ");
  Serial.print(Data.Pair10);
  Serial.print(", ");
  Serial.print(Data.Pair11);
  Serial.print(", ");
  Serial.println(Data.Pair12);
}

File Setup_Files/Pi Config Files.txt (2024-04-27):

To allow the ESP32's to communicate with the Pi, or another PC run the following commands. Otherwise the Serial Port won't appear

sudo systemctl stop brltty-udev.service
sudo systemctl mask brltty-udev.service
sudo systemctl stop brltty.service
sudo systemctl disable brltty.service

for the system to work with nomachine without needing a connection to a monitor
sudo systemctl set-default multi-user
to go back to standard
sudo systemctl set-default graphical.target
to boot the gui on a monitor
sudo systemctl start gdm3

note: by default access to the ttyusb is denied.
To rectify this

sudo usermod -a -G tty yourname
sudo usermod -a -G dialout yourname

sudo usermod -a -G tty ian
sudo usermod -a -G dialout ian 

where yourname is dev

sudo nano ~/.bashrc
paste this line at the bottom, saves a lot of menace with the ros2 sourcing.
source /home/dev/RaspberryCore/CoreRaspberry/install/local_setup.bash

And this line to set the ros domain ID

export ROS_DOMAIN_ID=32
echo -e "ROS_DOMAIN_ID: \033[32m$ROS_DOMAIN_ID\033[0m"

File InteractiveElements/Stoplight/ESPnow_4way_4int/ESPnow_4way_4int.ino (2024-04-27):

#include <ESP32Servo.h>
#include <esp_now.h>
#include <WiFi.h>

#define green_pwr 120
#define yellow_pwr 1//255
#define blue_pwr 120
#define white_pwr 120
#define red_pwr 255

//[Red,Yellow,Green,White,Blue]
//LEDS controlled by array*respective pwr.  so if you want indivitual control, change powers to 1, and set the 0-255 in the
static int S0[] = {0,0,0,0,0};  //off
static int S1[] = {1,0,0,1,1}; //stop
static int S2[] = {0,1,0,0,0}; //caution
static int S3[] = {0,0,1,0,1}; //go
static int S4[] = {0,0,0,1,0}; //white light 
static int S5[] = {0,0,0,0,1}; //blue Light
static int S6[] = {0,1,0,1,0}; //opt
static int S7[] = {0,0,1,0,1}; //opt
static int S8[] = {0,0,1,1,1}; //opt
static int S9[] = {0,1,0,1,1}; //opt
static int S10[] = {1,1,1,1,1}; //opt

typedef struct DataStruct {
  int Pair1;
  int Pair2;
  int Pair3;
  int Pair4;
  int Pair5;
  int Pair6;
  int Pair7;
  int Pair8;
  int Pair9;
  int Pair10;
  int Pair11;
  int Pair12;
  int Pair13;
  int Pair14;
  int Pair15;
  int Pair16;
}DataStruct;
DataStruct Data;

int Ctrl1 = 0;
int Ctrl2 = 0;
int Ctrl3 = 0;
int Ctrl4 = 0;

/* PCB Connections/ V1
Connector 1      Connector 2     Connector 3      Connector 4
Red 12               15              6                21 
Yellow 14             4            Linked 1           Linked 2
Green 26             18            Linked 1           Linked 2
White  25            19              8                23
Blue 27               5              7                22
*/
//Idiot ME, using 6,7,8,9,10,11 BAD IDEA!
//Good Pins  4 13 14 maybe 15 16 17 18 19 21 22 23 25 26 27 32 33
//25 flashes before first write for some reason.
/* PCB Connections/ V2
Connector 1      Connector 2     Connector 3      Connector 4
Red 12               32              16                21 
Yellow 14             4            Linked 1           Linked 2
Green 26             18              13                25
White  33            19              17                23
Blue 27               5              16                22
*/


#define redPin 12
#define yellowPin 14
#define greenPin 26
#define whitePin 33//25
#define bluePin 27



#define redPin2 32//15
#define yellowPin2 4
#define greenPin2 18
#define whitePin2 19
#define bluePin2 5


#define redPin3 13//13
#define greenPin3 15//18
#define whitePin3 17//16
#define bluePin3 16//17



#define redPin4 21
#define greenPin4 25//18
#define whitePin4 23
#define bluePin4 22





  int red;
  int yellow;
  int green;
  int white;
  int blue;

enum Color {Off, Red, Yellow, Green,White,Blue, Green_White, Green_Blue, Red_White, Red_Blue, All,Glow};
Color color;


int timer = 0;



void setup() {
  Serial.begin(115200);
  pinMode(redPin, OUTPUT);
  pinMode(greenPin, OUTPUT);
  pinMode(bluePin, OUTPUT);
  pinMode(yellowPin, OUTPUT);
  pinMode(whitePin, OUTPUT);

  pinMode(redPin2, OUTPUT);
  pinMode(greenPin2, OUTPUT);
  pinMode(bluePin2, OUTPUT);
  pinMode(yellowPin2, OUTPUT);
  pinMode(whitePin2, OUTPUT);

  pinMode(redPin4, OUTPUT);
  pinMode(greenPin4, OUTPUT);
  pinMode(whitePin4, OUTPUT);
  pinMode(bluePin4, OUTPUT);

  pinMode(redPin3, OUTPUT);
  pinMode(greenPin3, OUTPUT);
  pinMode(whitePin3, OUTPUT);
  pinMode(bluePin3, OUTPUT);
  



//Esp Init Code
  WiFi.mode(WIFI_STA);

  //Init ESP-NOW
  if (esp_now_init() != ESP_OK) {
    Serial.println("Error initializing ESP-NOW");
    return;}
  esp_now_register_recv_cb(OnDataRecv);
  analogWrite(whitePin, 0); // silences the flashing white light on output 25.
 LEDinit();
}


void loop() {
if(color == Glow){
    glowfade();
}

}


void OnDataRecv(const uint8_t * mac, const uint8_t *incomingData, int len) {
  memcpy(&Data, incomingData, sizeof(Data));
  /*Serial.print("Bytes received: ");
  Serial.println(len);
  Serial.print("Relevant Data: ");*/
  Ctrl1 = Data.Pair1;
  Ctrl2 = Data.Pair2;
  Ctrl3 = Data.Pair3;
  Ctrl4 = Data.Pair4;
  /*Serial.print(Ctrl1);
  Serial.print(", ");
  Serial.print(Ctrl2);
  Serial.print(", ");
  Serial.print(Ctrl3);
  Serial.print(", ");
  Serial.println(Ctrl4);*/

  activateLight(Ctrl4, redPin4, yellowPin2, greenPin4, whitePin4, bluePin4 );
  activateLight(Ctrl3, redPin3, yellowPin, greenPin3, whitePin3, bluePin3 );

  activateLight(Ctrl2, redPin2, yellowPin2, greenPin2, whitePin2, bluePin2);
  activateLight(Ctrl1, redPin, yellowPin, greenPin, whitePin, bluePin );

 // printDataStructure(Data);


 




}

void printDataStructure(const DataStruct &data) {
    char lines[4][50], dataArray[50];

    // Format lines with message and variables
    sprintf(lines[0], "4_way:------[ %d,  %d,  %d, %d]", data.Pair1, data.Pair2, data.Pair3, data.Pair4);
    sprintf(lines[1], "3_way:----- [ %d,  %d,  %d, %d]", data.Pair5, data.Pair6, data.Pair7, data.Pair8);
    sprintf(lines[2], "Train_Xing:-[ %d,  %d,  %d, %d]", data.Pair9, data.Pair10, data.Pair11, data.Pair12);
    sprintf(lines[3], "Aux:------- [ %d,  %d,  %d, %d]", data.Pair13, data.Pair14, data.Pair15, data.Pair16);

    // Format the array at the end
    sprintf(dataArray, "Data array: [%d, %d, %d, %d, %d, %d, %d, %d, %d, %d, %d, %d, %d, %d, %d, %d]", 
            data.Pair1, data.Pair2, data.Pair3, data.Pair4,
            data.Pair5, data.Pair6, data.Pair7, data.Pair8,
            data.Pair9, data.Pair10, data.Pair11, data.Pair12,
            data.Pair13, data.Pair14, data.Pair15, data.Pair16);

    // Print the lines to serial
    for (int i = 0; i < 4; ++i) {
        Serial.println(lines[i]);
    }
    Serial.println(dataArray);
}

void activateLight(int ctrl ,int rpin, int ypin, int gpin, int wpin, int bpin){
  Color_Convert_int(ctrl);
  Color_state();
  setColor(rpin, ypin, gpin, wpin, bpin);
}

void setColor(int rpin, int ypin, int gpin, int wpin, int bpin) {
  analogWrite(rpin, red);
  analogWrite(gpin, green);
  analogWrite(bpin, blue);
  //analogWrite(ypin, yellow);
  digitalWrite(ypin, yellow);
  analogWrite(wpin, white);
}

void Color_Convert_int(int value){
switch (value){
  case 0:
  color = Off;
  break;
  case 1:
  color = Red;
  break;
    case 2:
  color = Yellow;
  break;
    case 3:
  color = Green;
  break;
    case 4:
  color = White;
  break;
    case 5:
  color = Blue;
  break;
    case 6:
  color = Green_White;
  break;
    case 7:
  color = Green_Blue;
  break;
    case 8:
  color = Red_White;
  break;
    case 9:
  color = Red_Blue;
  break;
    case 10:
  color = All;
  break;
  case 11:
  color = Glow;
}}

void Color_state(){

switch (color){
    case Off:
    red = red_pwr*S0[0];
    yellow = yellow_pwr*S0[1];
    green = green_pwr*S0[2];
    white = white_pwr*S0[3];
    blue = blue_pwr*S0[4];
    break;

  case Red:
    red = red_pwr*S1[0];
    yellow = yellow_pwr*S1[1];
    green = green_pwr*S1[2];
    white = white_pwr*S1[3];
    blue = blue_pwr*S1[4];
    break;

case Yellow:
    red = red_pwr*S2[0];
    yellow = yellow_pwr*S2[1];
    green = green_pwr*S2[2];
    white = white_pwr*S2[3];
    blue = blue_pwr*S2[4];
    break;
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

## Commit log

2023-11-18 Redid serial work
    [Pi Config Files.txt]
2023-11-19 switched to pyserialxfer
2023-11-24 Kicad Work
    [Esp Controller-B_Cu.gbr, Esp Controller-B_Mask.gbr, Esp Controller-B_Paste.gbr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]
2023-11-24 added map frame id
2023-11-27 Pcb Stuff
    [3X2 V2.stl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]
2023-12-01 updated config for Nomachine
    [Pi Config Files.txt]
2023-12-01 more setup file updates
    [Pi Config Files.txt]
2023-12-13 Update to ESP Pcb
    [Esp Controller-B_Cu.gbr, Esp Controller-B_Mask.gbr, Esp Controller-B_Paste.gbr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]
2023-12-14 NEW Pcb
    [3X2 V2.stl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]
2023-12-19 updated PCB
2023-12-19 corrected serial port detect
    [esp_serial.py]
2023-12-19 Updated for USB filter
2023-12-20 added servo direct controller
2024-01-16 modified pcb
    [Esp Controller-B_Cu.gbr, Esp Controller-B_Mask.gbr, Esp Controller-B_Paste.gbr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]
2024-01-18 added ESP driver
2024-02-15 mods, and added pose control files
    [Light Main Body.stl]
2024-02-15 copied worlds directory
    [Light Main Body.stl]
2024-02-15 moved worlds again
    [Light Main Body.stl]
2024-02-15 try again
    [Light Main Body.stl]
2024-02-15 moved markers
    [Light Main Body.stl]
2024-02-16 added 0 pose case
2024-02-16 renamed file
    [light.stl]
2024-02-16 fused nodes to node
2024-02-16 added threading for multi nodal work
2024-02-16 another threading try
2024-02-16 threading try 3
2024-02-16 back to stl
2024-02-16 wrong mesh size
    [light.stl]
2024-02-16 force update
    [light2.stl]
2024-02-16 pose file problems
    [light.stl]
2024-02-17 added printout
2024-02-17 more prints
2024-02-17 reducing printouts
2024-02-17 toublesome stl's
2024-02-17 aded markers folder
    [car.stl]
2024-02-17 added threading
2024-02-19 switched off python
2024-02-20 switched from 2 to 4 int
2024-02-21 updated track launch
2024-03-07 stupid colcon
    [Pi Config Files.txt]
2024-03-07 trying to get x11
    [Pi Config Files.txt]
2024-03-07 powershell tweaks undone
2024-03-07 parse problems
    [Pi Config Files.txt]
2024-03-14 fingers crossed
2024-03-14 changed timer and added multi spin
2024-03-14 needed 2nd timer
2024-03-14 switched none to empty
2024-03-14 another print
2024-03-14 different prints
2024-03-14 more print rework
2024-03-14 one more print cleanup
2024-03-15 added print
2024-03-17 added train crossing i hope
    [Light Main Body.stl]
2024-03-29 added 3d modelling folder
    [1-5.stl, 10 Pairs barrier Stands.3mf, 10-15.stl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]
2024-03-29 small oval added
    [Small Oval v2.obj]
2024-03-29 new light
    [light.stl]
2024-03-29 print added
2024-04-05 old was working, new adds reset and some stuff in mesh pub esp_Serial had wrong topic for train
    [esp_serial.py]
2024-04-09 print helps
2024-04-09 updating the odometry handle.
2024-04-09 debug print
2024-04-09 new prints
2024-04-12 forgotten commit
    [Four Way Long.obj, Long Oval.obj, Long Roundabout.obj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]
2024-04-12 new patterns
    [Pattern 4.stl, Pattern 5.stl, Pattern 6.stl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]
2024-04-12 new odometry
2024-04-12 print statements for testing
2024-04-13 xy rotation
    [untitled.stl]
2024-04-13 added a odometry reader
2024-04-27 updated schematic
    [Esp Controller.kicad_pcb, Esp Controller.kicad_sch]
2024-04-27 file move
    [Full Oval Export Testing v1.obj, Full Oval Export Testing v2.obj, RR Barrier only.obj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]
2024-04-27 moved up one layer
    [3X2 V2.stl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]
2024-04-27 Added Yolo Package
    [_1-5 (Entrance).219effff-f473-44bc-a75d-e1218fa6c62f.f3d, _1-5 (Entrance).922a9380-cdaf-486c-86eb-b796c98b9d1c.f3d, _1-5 (Entrance).922a9380-cdaf-486c-86eb-b79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]
